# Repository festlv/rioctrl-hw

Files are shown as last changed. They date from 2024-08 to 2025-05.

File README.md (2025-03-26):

# rioctrl- a modular hardware for riocore

rioctrl is modular open source CNC controller hardware for [riocore](https://github.com/multigcs/riocore/).

It consists of a main FPGA controller board which has 6 slots for various input/output modules.

At this time, the following modules have been designed:

* [rioctrl-controller](rioctrl-controller/README.md): Lattice ECP5 based controller board
* [rioctrl-stepdir4](rioctrl-stepdir4/README.md): 4 axis step/dir output interface
* [rioctrl-quadenc4](rioctrl-quadenc4/README.md): 4 axis quadrature encoder (ABZ) input
* [rioctrl-shifio](rioctrl-shiftio/README.md): 16 digital inputs, 16 digital outputs (PNP)
* breakouts/lichuan-lc10: breakout board that allows connecting Lichuan LC10 series servo to stepdir4 and quadenc4 module (via off-the-shelf RJ45 cables)
* breakouts/rj45-screw-terminals: breakout board from RJ45 cable to screw terminals
* breakouts/ditron-dc11-encoder: breakout board from RJ45 cable to Ditron DC11 glass scale optical encoder (DB9)

# Current state of the hardware design

The following hardware has been built and tested to be working:

* rioctrl-controller v1.0: minor rework was needed (remove a diode, rotate Y1 by 90 degrees). Fixed in v1.1.
* rioctrl-stepdir4 v1.0: electrically working, mechanically a connector was offset by 4 mm, fixed in v1.1.
* rioctrl-shiftio: working as designed.
* rioctrl-quadencz: working as designed (with the caveat that it's only compatible with differential/RS422 encoders).
* breakouts/ditron-dc11-encoder: working as designed, tested with Ditron DC11 encoder with RS422 output option.
* breakouts/rj45-screw-terminals: working as designed.
* breakouts/lichuan-lc10: step/dir/enable working as designed, GPIOs not tested yet.

## Known issues

* External override for slot enable is slow to turn off stepdir enable signals. Need to scope this a bit, but it's either due to U14 output being
  tri-stated or the capacitance of +24V_EN lines powering the enable signals for some additional time.
# Pretty images

### rioctrl-controller
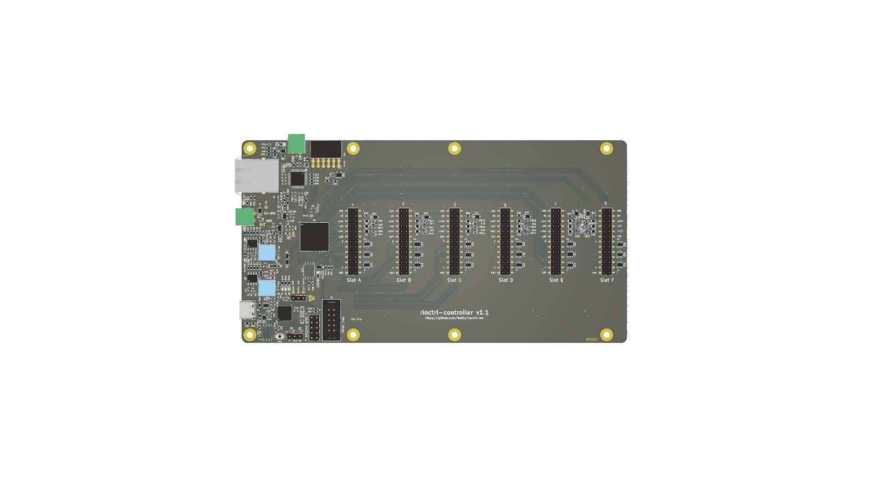
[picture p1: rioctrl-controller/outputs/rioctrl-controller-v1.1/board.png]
rioctrl-controller


### rioctrl-stepdir4
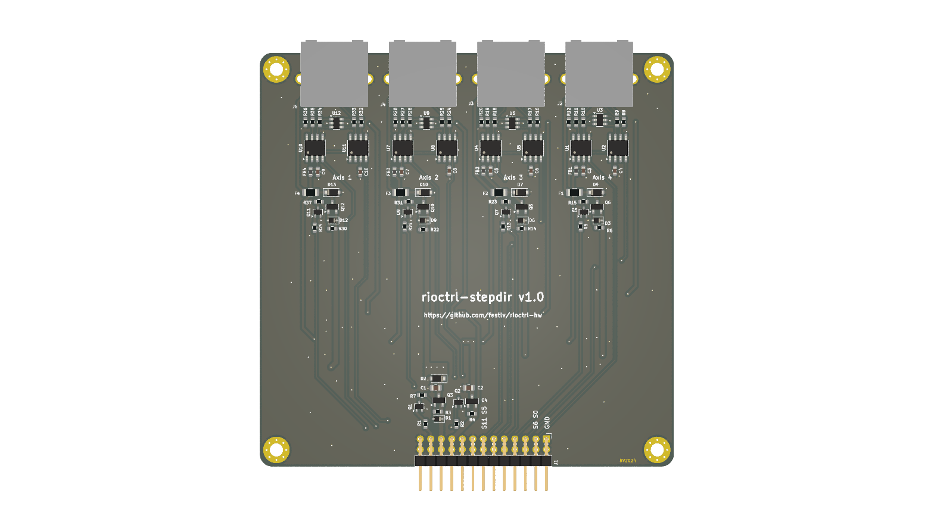
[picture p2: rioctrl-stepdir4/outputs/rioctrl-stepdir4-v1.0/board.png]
rioctrl-stepdir4


### rioctrl-quadenc4
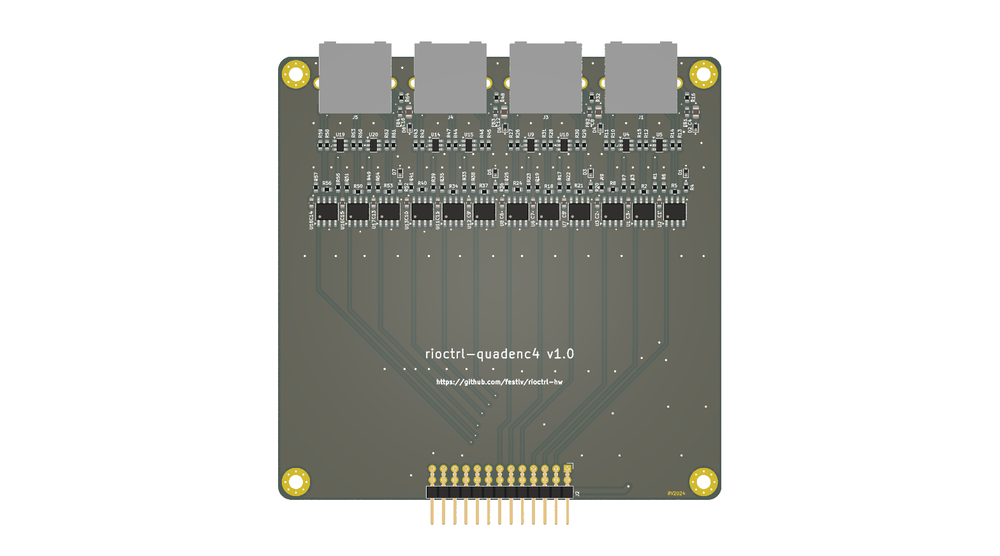
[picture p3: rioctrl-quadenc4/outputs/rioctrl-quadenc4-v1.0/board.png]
rioctrl-quadenc4


### rioctrl-shiftio
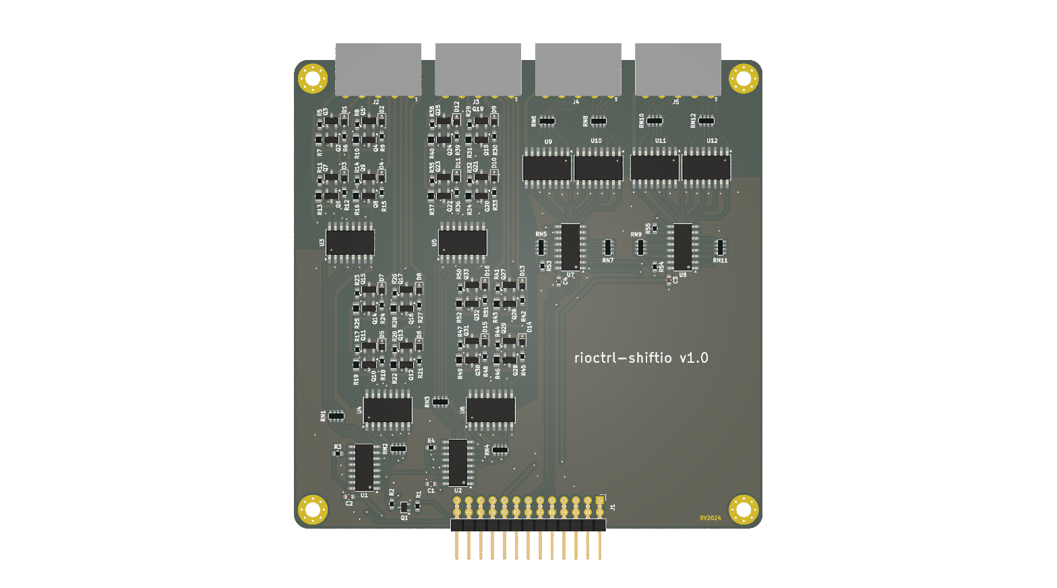
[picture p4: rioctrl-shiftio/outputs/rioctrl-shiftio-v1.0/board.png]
rioctrl-shiftio


### breakouts/lichuan-lc10
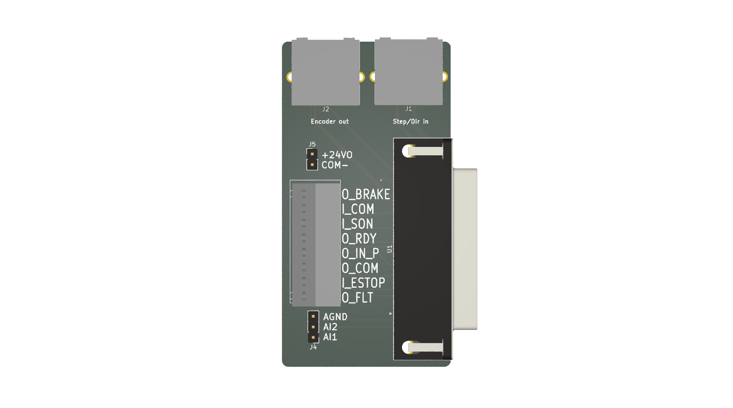
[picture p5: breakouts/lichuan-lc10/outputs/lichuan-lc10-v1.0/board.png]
breakouts/lichuan-lc10


### breakouts/rj45-screw-terminals
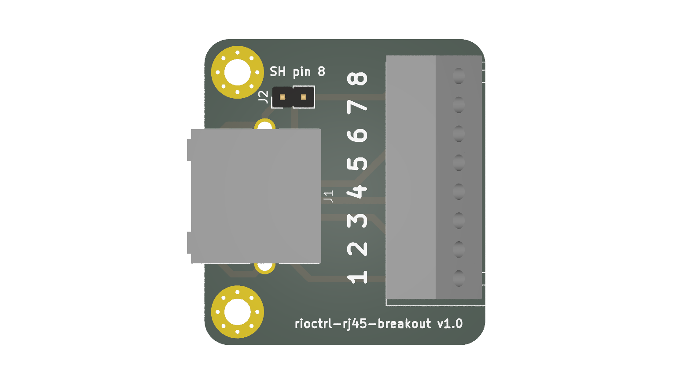
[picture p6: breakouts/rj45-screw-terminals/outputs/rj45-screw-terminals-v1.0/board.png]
breakouts/rj45-screw-terminals


## build.py

There is a `build.py` script that publishes outputs to each module `outputs` directory. It uses `<module>/version` file to
determine the current version, which should be updated accordingly.

For 3D renders of the boards, kicad-nightly package is needed, as the currently stable kicad version does not have board rendering functionality available from command line.

# License

The hardware designs in this repository are licensed under [CERN Open Hardware Licence Version 2 - Strongly Reciprocal](LICENSE.md).

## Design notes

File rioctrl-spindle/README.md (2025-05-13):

# rioctrl-spindle
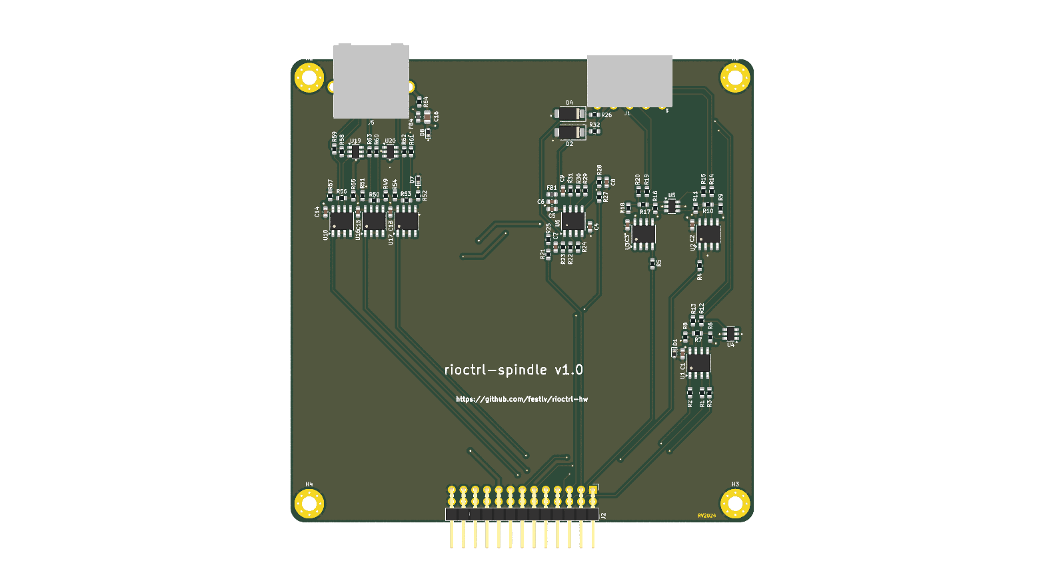
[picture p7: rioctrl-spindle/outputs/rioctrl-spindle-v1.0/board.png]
rioctrl-spindle


This module provides:
* 2 analog outputs (0..10V)
* RS-485 interface for Modbus
* RS-422 interface (for full-duplex serial communication, pending software support)
* Differential encoder interface

__Only analog outputs and Modbus has been tested!__

## Pinout

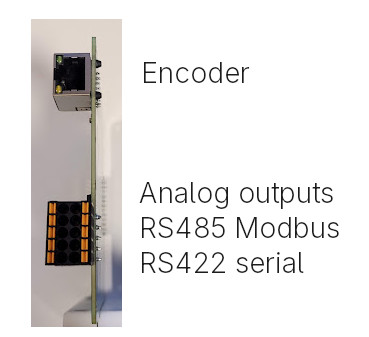
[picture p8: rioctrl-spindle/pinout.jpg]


| | |
|---|---|
| AIN0  | GND |
| AIN1  | SER_TX_A |
| MODBUS_A | SER_TX_B |
| MODBUS_B | SER_RX_A |
| x | SER_RX_B |

# Changelog

## v1.0
Initial released version.

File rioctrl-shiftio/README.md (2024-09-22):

# rioctrl-shiftio
rioctrl-shiftio

This module provides the following IOs:
* 16 opto-isolated digital outputs (PNP, external voltage input 5-24V in two groups). Each output is capable of sourcing ~0.6A of current and has over-current protection.
* 16 opto-isolated digital inputs (12-24V, both sourcing and sinking connections are possible).

Due to slot width limitations, each group of outputs (4 in total) are fitted with spring-type pluggable terminal blocks (LCSC part number:
[C2908401](https://www.lcsc.com/product-detail/Pluggable-System-Terminal-Block_JILN-JL15EDGKNH-35005B01_C2908401.html)).

# Pinout
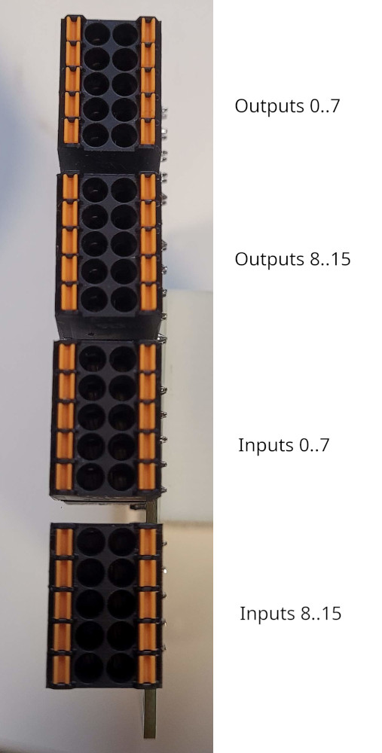
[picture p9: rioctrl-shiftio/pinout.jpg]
pinout


## Pinout of output blocks

VCC is 5..24V DC. Each of the output blocks has a separate power supply, so for example
one block can be 5V outputs and another one- 24VDC.

| VCC  | GND  |
|---|---|
| 0 | 1 |
| 2 | 3 |
| 4 | 5 |
| 6 | 7 |

| VCC | GND |
|-----|-----|
| 8 | 9 |
| 10  | 11  |
| 12  | 13  |
| 14  | 15  |

## Pinout of input blocks

Common input can be either ground, or positive voltage of 12..24VDC for sourcing or 
sinking type outputs.

Limited testing has shown that inputs also work at 5V output level, but that's not really guaranteed with the
values of components in current design.

| | Common |
|---|---|
| 0 | 1 |
| 2 | 3 |
| 4 | 5 |
| 6 | 7 |

|  | Common |
|-----|---|
| 8 | 9 |
| 10  | 11 |
| 12  | 13 |
| 14  | 15 |

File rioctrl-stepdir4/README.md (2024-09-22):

# rioctrl-stepdir4
rioctrl-stepdir4

This module provides 4 axis of step/dir/enable signals.
* Step/dir signals are differential 5V.
* Enable signal is at the same voltage as controller's DC input.

The connectors are RJ45 (intended use is either with motor-drive specific breakout board or a generic screw-terminal type breakout board).

RJ45 green LED is wired to enable signal.

## Pinout (when using breakouts/rioctrl-rj45-breakout):

| Pin | Signal |
|-----|---|
| 1 | Step + |
| 2 | Step - |
| 3 | Dir -  |
| 4 | Enable |
| 5 | GND |
| 6 | Dir -  |
| 7 | GND |
| 8 | GND |

# Changelog

## v1.1
* Fixed slot's pin-header position (was offset by 4 mm)
* Rename silkscreen labels from axis 1..4 to join 0..3 to match riocore/LinuxCNC convention
 
## v1.0
Initial released version.

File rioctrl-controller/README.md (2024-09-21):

# rioctrl-controller
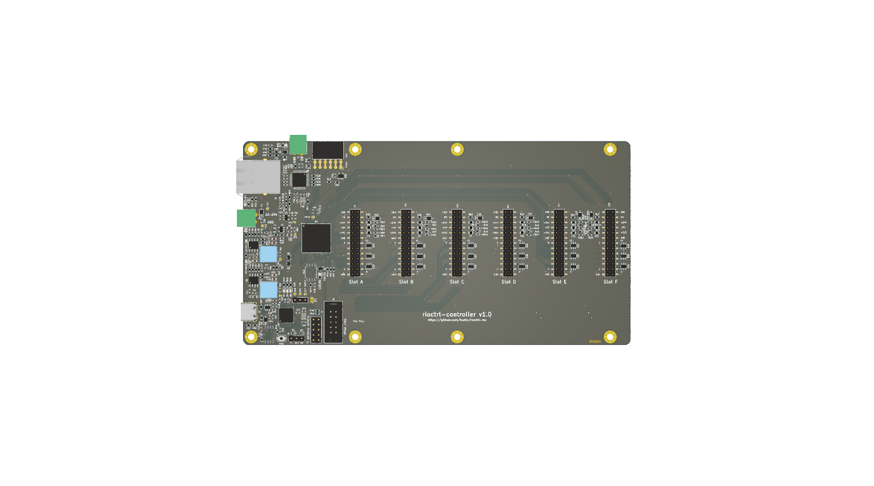
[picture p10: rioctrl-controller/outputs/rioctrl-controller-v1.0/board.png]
rioctrl-controller


The heart of controller is Lattice ECP5-series FPGA with 25k logic cells.

It has the following inputs/outputs:

* RJ45 Ethernet interface to PC (via Wiznet W5500)
* USB TypeC for re-flashing the FPGA (using RP2040 microcontroller with [pico-dirtyJtag](https://github.com/phdussud/pico-dirtyJtag) firmware)
* 12-24V DC input for powering the FPGA and basic slot hardware
* E-Stop signal that inhibits slot outputs in hardware, independant of FPGA gateware
* PMOD header for future expansion (e.g. controlling the board via SPI from RaspberryPi or something)
* JTAG header for FPGA debugging
* SWD header for JTAG probe debugging :)
* Six 2x13 pin 2.54mm sockets for slots (each has 12 FPGA signals, additional shared enable signal, +3.3V, +5V and input DC power)

Slot specification:
* Preferred slot PCB size: 100x100mm
* There are 12 FPGA signals wired to each slot, all of them are 3.3V.
* The following power rails are wired to each slot:
  * 3.3V
  * 5V
  * Input DC (12-24V)
* Each slot has an enable signal, whose state is a logical AND of FPGA enable output (watchdog-protected when using riocore) and external EStop input.
* Each slot **MUST** inhibit it's outputs in hardware when the enable signal is low.

# Changelog

## V1.0 -> V1.1
* Fix Y1 orientation
* DNP the USB VBUS -> 5V diode (it's useless, as 3.3V rails are generated by input voltage)
* Change LED:OK to green
 
# Bringup notes

* Build and flash the default configuration of pico-dirtyJtag (hold the boot button while turning on 12V power, then connect USB and flash via copying .uf2 to removable drive).
* Try to see if the FPGA is detected:
```
$ openFPGALoader -c dirtyJtag --detect

Jtag frequency : requested 6000000Hz -> real 6000000Hz
index 0:
	idcode 0x41111043
	manufacturer lattice
	family ECP5
	model  LFE5U-25
	irlength 8
```

# Version 1.0 rework
* Y1 needs to be rotated 90 degrees (again, sigh)
* Remove the D9 diode (USB power does not work anyway)
* Change D12 to green LED

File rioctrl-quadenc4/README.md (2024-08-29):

# rioctrl-quadenc4
rioctrl-quadenc4

This module provides 4 axis of differential quadrature encoder inputs, intended for 5V differential output encoders.
Each axis has A, B and Z inputs.

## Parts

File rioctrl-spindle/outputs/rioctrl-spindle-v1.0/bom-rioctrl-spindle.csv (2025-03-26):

Refs | Value | Footprint | Manufacturer | MPN | Qty | DNP | LCSC#
C1-C3,C6,C13-C15 | 0.1uF | Capacitor_SMD:C_0603_1608Metric |  |  | 7 |  | -- mixed values --
C4,C8 | 3.3nF | Capacitor_SMD:C_0603_1608Metric |  |  | 2
C5 | 10uF | Capacitor_SMD:C_0603_1608Metric |  |  | 1
C7,C9 | 10nF | Capacitor_SMD:C_0603_1608Metric |  |  | 2
C16 | 10uF | Capacitor_SMD:C_0805_2012Metric |  | GRM21BR61H106KE43L | 1 |  | C440198
D1,D7 | BSD5C031V | Diode_SMD:D_SOD-523 | BORN | BSD5C031V | 2 |  | C151984
D2,D4 | SMAJ10A | Diode_SMD:D_SMA |  |  | 2
D8 | PESD5V0S1BBN | Diode_SMD:D_SOD-523 | BORN | PESD5V0S1BBN | 1 |  | C314264
FB1,FB4 | FB_100R_3A | Inductor_SMD:L_0603_1608Metric | Sunlord | UPZ1608E101-3R0TF | 2 |  | C96995
J1 | TERM-BLK-02x05 | hadv-connectors:JL15EDGRHC-35005B02 | JILN | JL15EDGRHC-35005B02 | 1 |  | C2908411
J2 | Conn_02x13_Odd_Even | Connector_PinHeader_2.54mm:PinHeader_2x13_P2.54mm_Horizontal |  |  | 1 |  | C2894993
J5 | RJ45_LED_Shielded | hadv-connectors:R-RJ45R08P-C000 | Ckmtw(Shenzhen Cankemeng) | R-RJ45R08P-C000 | 1 |  | C386757
R1,R6,R8,R9,R11,R16,R18,R49,R51,R52,R54,R55,R57 | 1K | Resistor_SMD:R_0603_1608Metric |  |  | 13 |  | C22548
R2-R5,R12-R15,R19,R20,R58-R63 | 10R | Resistor_SMD:R_0603_1608Metric |  |  | 16 |  | C109318
R7,R10,R17,R50,R53,R56 | 120R | Resistor_SMD:R_0603_1608Metric |  |  | 6 |  | C114640
R21-R24,R27,R29-R31 | 10K | Resistor_SMD:R_0603_1608Metric |  |  | 8
R25,R28 | 100K | Resistor_SMD:R_0603_1608Metric |  |  | 2
R26,R32 | 50R | Resistor_SMD:R_0603_1608Metric |  |  | 2
R64 | 0R | Resistor_SMD:R_0603_1608Metric |  |  | 1 |  | C95177
U1-U3,U16-U18 | CS48505S | Package_SO:SOIC-8_3.9x4.9mm_P1.27mm | Chipanalog | CS48505S | 6 |  | C3202824
U4,U5,U19,U20 | USBLC6-4SC6 | Package_TO_SOT_SMD:SOT-23-6 | TECH PUBLIC | USBLC6-4SC6 | 4 |  | C5197386
U6 | LM358DT | Package_SO:SO-8_3.9x4.9mm_P1.27mm | STMicroelectronics | LM358DT | 1 |  | C9418

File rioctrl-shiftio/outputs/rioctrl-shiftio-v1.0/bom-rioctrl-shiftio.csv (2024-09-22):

Refs | Value | Footprint | Manufacturer | MPN | Qty | DNP | LCSC#
C1-C4 | 0.1uF | Capacitor_SMD:C_0603_1608Metric |  |  | 4 |  | C14663
D1-D16 | 1N4007WS | Diode_SMD:D_SOD-323F | MKSEMI | 1N4007WS | 16 |  | C7528872
J1 | Conn_02x13_Odd_Even | Connector_PinHeader_2.54mm:PinHeader_2x13_P2.54mm_Horizontal |  |  | 1 |  | C2894993
J2-J5 | TERM-BLK-02x05 | hadv-connectors:JL15EDGRHC-35005B02 | JILN | JL15EDGRHC-35005B02 | 4 |  | C2908411
Q1 | BSS138W | Package_TO_SOT_SMD:SOT-323_SC-70 | Jiangsu Changjing Electronics Technology Co., Ltd. | BSS138W | 1 |  | C504052
Q2,Q4,Q6,Q8,Q10,Q12,Q14,Q16,Q18,Q20,Q22,Q24,Q26,Q28,Q30,Q32 | MMBT3906 | Package_TO_SOT_SMD:SOT-23 | TWGMC | MMBT3906 | 16 |  | C727128
Q3,Q5,Q7,Q9,Q11,Q13,Q15,Q17,Q19,Q21,Q23,Q25,Q27,Q29,Q31,Q33 | AO3401A | Package_TO_SOT_SMD:SOT-23 | UMW | AO3401A | 16 |  | C347476
R1,R3,R4,R6,R9,R12,R15,R18,R21,R24,R27,R30,R33,R36,R39,R42,R45,R48,R51,R53-R55 | 10K | Resistor_SMD:R_0603_1608Metric |  |  | 22 |  | C98220
R2 | 4K7 | Resistor_SMD:R_0603_1608Metric |  |  | 1 |  | C99782
R5,R8,R11,R14,R17,R20,R23,R26,R29,R32,R35,R38,R41,R44,R47,R50 | 47K | Resistor_SMD:R_0603_1608Metric |  |  | 16 |  | C105579
R7,R10,R13,R16,R19,R22,R25,R28,R31,R34,R37,R40,R43,R46,R49,R52 | 1R | Resistor_SMD:R_0805_2012Metric |  |  | 16 |  | C131397
RN1-RN4 | 220R | Resistor_SMD:R_Array_Convex_4x0603 |  |  | 4 |  | C706474
RN5-RN12 | 4.12K | Resistor_SMD:R_Array_Convex_4x0603 |  |  | 8 |  | C728970
U1,U2 | 74HC595 | Package_SO:SO-16_3.9x9.9mm_P1.27mm | Nexperia | 74HC595D,118 | 2 |  | C5947
U3-U6,U9-U12 | ELQ3H4 | Package_SO:SOIC-16W_5.3x10.2mm_P1.27mm | Everlight Elec | ELQ3H4(TA)-G | 8 |  | C150957
U7,U8 | 74HC165 | Package_SO:SO-16_3.9x9.9mm_P1.27mm | Nexperia | 74HC165D,653 | 2 |  | C5613

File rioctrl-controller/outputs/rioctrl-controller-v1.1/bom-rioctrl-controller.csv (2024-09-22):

Refs | Value | Footprint | Manufacturer | MPN | Qty | DNP | LCSC#
C1-C3 | 10uF | Capacitor_SMD:C_0805_2012Metric | -- mixed values -- | -- mixed values -- | 3 |  | C440198
C4,C5,C12-C14,C21,C24,C25,C27-C32,C36,C40-C42,C55 | 0.1uF | Capacitor_SMD:C_0603_1608Metric | -- mixed values -- | -- mixed values -- | 19 |  | C14663
C6,C7 | 120pF | Capacitor_SMD:C_0603_1608Metric |  |  | 2 |  | C107035
C8,C9 | 0.012uF | Capacitor_SMD:C_0603_1608Metric |  |  | 2 |  | C282672
C10 | DNP | Capacitor_SMD:C_0603_1608Metric |  |  | 1 | DNP
C11 | 10uF/35V | Capacitor_SMD:C_0805_2012Metric | Murata | GRM21BR6YA106ME43L | 1 |  | C440198
C15-C18 | 47uF | Capacitor_SMD:C_0805_2012Metric |  | GRM21BR61H106KE43L | 4 |  | C6119904
C19,C20,C26 | 1uF | Capacitor_SMD:C_0603_1608Metric | -- mixed values -- | -- mixed values -- | 3 |  | C5673
C22,C23 | 10pF | Capacitor_SMD:C_0603_1608Metric | Yageo | CC0603JRNPO9BN100 | 2 |  | C106245
C33,C34 | 18pF | Capacitor_SMD:C_0603_1608Metric |  |  | 2 |  | C92671
C35,C39 | 10uF/6.3V | Capacitor_SMD:C_0603_1608Metric |  |  | 2 |  | C85713
C37,C46 | 10nF | Capacitor_SMD:C_0603_1608Metric |  |  | 2 |  | C100042
C38 | 4.7uF | Capacitor_SMD:C_0603_1608Metric |  |  | 1 |  | C1705
C43 | 22nF | Capacitor_SMD:C_0603_1608Metric |  |  | 1 |  | C77571
C44,C45 | 6.8nF | Capacitor_SMD:C_0603_1608Metric |  |  | 2 |  | C1631
C47-C54,C56-C67 | 0.1uF | Capacitor_SMD:C_0402_1005Metric |  |  | 20 |  | C56392
D1,D9 | DSS34 | Diode_SMD:D_SOD-123F | BORN | DSS34 | 2 | -- mixed values -- | C511866
D2,D4,D10,D17 | LED_RED | LED_SMD:LED_0603_1608Metric | Yongyu Photoelectric | SZYY0603R | 4 |  | C434419
D3,D11,D12 | LED_GREEN | LED_SMD:LED_0603_1608Metric | Yongyu Photoelectric | SZYY0603YG | 3 |  | C434423
D5 | LED_BLUE | LED_SMD:LED_0603_1608Metric | XINGLIGHT | XL-1608UBC-04 | 1 |  | C965807
D6-D8,D14,D19,D22,D25,D28,D31 | BSD5C031V | Diode_SMD:D_SOD-523 | BORN | BSD5C031V | 9 |  | C151984
D13,D18,D21,D24,D27,D30 | SMF24A | Diode_SMD:D_SOD-123F | Shandong Jingdao Microelectronics | SMF24A | 6 |  | C169430
D15,D16,D20,D23,D26,D29,D32 | PESD5V0S1BBN | Diode_SMD:D_SOD-523 | BORN | PESD5V0S1BBN | 7 |  | C314264
F1-F18 | SMD0805B050TF | Fuse:Fuse_0805_2012Metric | Yageo | SMD0805B050TF | 18 |  | C269104
FB1-FB25 | FB_100R_3A | Inductor_SMD:L_0603_1608Metric | Sunlord | UPZ1608E101-3R0TF | 25 |  | C96995
J1,J7 | TERM-BLK-2H | Connector_Phoenix_MC:PhoenixContact_MC_1,5_2-G-3.5_1x02_P3.50mm_Horizontal | Cixi Kefa Elec | KF2EDGR-3.5-2P | 2 |  | C441171
J2,J5 | PIN_HEADER_3V | Connector_PinHeader_2.54mm:PinHeader_1x03_P2.54mm_Vertical | Boom Precision Elec | C49257 | 2 |  | C49257
J3 | TYPE-C-31-M-12 | hadv-connectors:USB_C_Receptacle_HRO_TYPE-C-31-M-12 | Korean Hroparts | TYPE-C-31-M-12 | 1 |  | C165948
J4 | Conn_02x05_Odd_Even | Connector_PinHeader_2.54mm:PinHeader_2x05_P2.54mm_Vertical |  |  | 1 | DNP
J6 | RJ45_Pulse_J0011D21BNL | hadv-connectors:RJ45_J0011D21BNL | Pulse | J0011D21BNL | 1 |  | C455444
J8 | Conn_02x05_PH | Connector_IDC:IDC-Header_2x05_P2.54mm_Vertical |  |  | 1 |  | C5665
J9,J11-J15 | Conn_02x13_Odd_Even | Connector_PinSocket_2.54mm:PinSocket_2x13_P2.54mm_Vertical_SMD |  |  | 6 |  | C3975158
J10 | Conn_02x06_Odd_Even | Connector_PinSocket_2.54mm:PinSocket_2x06_P2.54mm_Horizontal |  |  | 1 |  | C2897426
L1 | MLP2012S4R7MT0S1 | Inductor_SMD:L_0805_2012Metric | TDK | MLP2012S4R7MT0S1 | 1 |  | C87543
L2,L3 | PSPMAA0805-220M-ANP | hadv-inductors:SMD_INDUCTOR_8x8.5x5mm | PROD Tech | PSPMAA0805-220M-ANP | 2 |  | C2962887
Q1-Q4 | BSS138W | Package_TO_SOT_SMD:SOT-323_SC-70 | Jiangsu Changjing Electronics Technology Co., Ltd. | BSS138W | 4 |  | C504052
R1,R17,R23,R27,R29-R32,R44-R49,R54 | 10K | Resistor_SMD:R_0603_1608Metric | -- mixed values -- | -- mixed values -- | 15 |  | C98220
R2,R3,R5,R7,R10 | 47K | Resistor_SMD:R_0603_1608Metric | -- mixed values -- |  | 5 |  | C105579
R4,R6 | 220K | Resistor_SMD:R_0603_1608Metric |  |  | 2 |  | C123420
R8,R9 | 3.47K | Resistor_SMD:R_0603_1608Metric |  |  | 2 |  | C273778
R11 | 56.2K | Resistor_SMD:R_0603_1608Metric | Yageo | RC0603FR-0710KL | 1 |  | C98220
R12,R14,R26 | 100K | Resistor_SMD:R_0603_1608Metric | -- mixed values -- | -- mixed values -- | 3 |  | C112314
R13 | 19.1K | Resistor_SMD:R_0603_1608Metric |  |  | 1 |  | C173754
R15 | 32K | Resistor_SMD:R_0603_1608Metric |  |  | 1 |  | C861839
R16,R18,R19,R28,R55 | 1K | Resistor_SMD:R_0603_1608Metric | -- mixed values -- | -- mixed values -- | 5 |  | C22548
R20-R22 | 5.11K | Resistor_SMD:R_0603_1608Metric | Yageo | RC0603FR-075K11L | 3 |  | C112314
R24 | 1M | Resistor_SMD:R_0603_1608Metric |  |  | 1 |  | C107698
R25 | 12.4K | Resistor_SMD:R_0603_1608Metric |  |  | 1 |  | C22865
R33,R34,R50-R52,R56 | 330R | Resistor_SMD:R_0603_1608Metric |  |  | 6 |  | C105881
R35-R38 | 0R | Resistor_SMD:R_0603_1608Metric |  |  | 4 |  | C95177
R39,R40,R42,R43 | 49.9R | Resistor_SMD:R_0603_1608Metric |  |  | 4 |  | C114625
R41 | 10R | Resistor_SMD:R_0603_1608Metric |  |  | 1 |  | C109318
R53,R58-R62 | 100R | Resistor_SMD:R_0603_1608Metric |  |  | 6 |  | C105588
R57,R63 | 4K7 | Resistor_SMD:R_0603_1608Metric |  |  | 2 |  | C99782
SW1 | SW_PUSH_SMALL | hadv-ui:SW_SPST_AR02016 | XUNPU | TS-1088-AR02016 | 1 |  | C720477
U1 | TD6811 | Package_TO_SOT_SMD:SOT-23-5 | Techcode | TD6811 | 1 |  | C189486
U2,U3 | TPS54335ADDAR | Package_SO:SOIC-8-1EP_3.9x4.9mm_P1.27mm_EP2.29x3mm_ThermalVias | Texas Instruments | TPS54335ADDAR | 2 |  | C58928
U4 | NCP114ASN250T1G | Package_TO_SOT_SMD:SOT-23-5 | Onsemi | NCP114ASN250T1G | 1 |  | C892030
U5,U10 | W25Q16JVSS | Package_SO:SOIC-8_5.23x5.23mm_P1.27mm | Winbond | W25Q16JVSSIQ | 2 |  | C82317
U6 | USBLC6-4SC6 | Package_TO_SOT_SMD:SOT-23-6 | TECH PUBLIC | USBLC6-4SC6 | 1 |  | C5197386
U7 | RP2040 | hadv-mcu:RP2040-QFN-56 | Raspberry Pi | RP2040 | 1 |  | C2040
U8 | W5500 | Package_QFP:LQFP-48_7x7mm_P0.5mm |  |  | 1 |  | C32843
U9 | ECP5U_45_CABGA256 | Package_BGA:BGA-256_14.0x14.0mm_Layout16x16_P0.8mm_Ball0.45mm_Pad0.32mm_NSMD | Lattice | LFE5U-12F-6BG256C | 1 |  | C1550762
U11-U13,U15-U29 | SRV05-4 | Package_TO_SOT_SMD:SOT-23-6 | UMW(Youtai Semiconductor Co., Ltd.) | SRV05-4.TCT | 18 |  | C2687126
U14 | SN74LVC1G125DBV | Package_TO_SOT_SMD:SOT-23-5 | Texas Instruments | SN74LVC1G125DBVR | 1 |  | C23654
X1 | OSC_25MHz | Oscillator:Oscillator_SMD_EuroQuartz_XO32-4Pin_3.2x2.5mm | YXC Crystal Oscillators | OT322525MJBA4SL | 1 |  | C669088
Y1 | Crystal_12MHz | Crystal:Crystal_SMD_2520-4Pin_2.5x2.0mm | TAE(Zhejiang Abel Elec) | TXM12M0004252DBCEO00T | 1 |  | C284154
Y2 | Crystal_25MHz | Crystal:Crystal_SMD_2520-4Pin_2.5x2.0mm | Yajingxin | TXM25M0004252DBCEO00T | 1 |  | C284164

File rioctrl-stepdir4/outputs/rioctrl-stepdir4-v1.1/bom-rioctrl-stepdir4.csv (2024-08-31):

Refs | Value | Footprint | Manufacturer | MPN | Qty | DNP | LCSC#
C1,C2 | 10uF | Capacitor_SMD:C_0805_2012Metric |  | GRM21BR61H106KE43L | 2 |  | C440198
C3-C10 | 0.1uF | Capacitor_SMD:C_0603_1608Metric |  |  | 8 |  | C14663
D1,D3,D6,D9,D12 | BZT52C10S | Diode_SMD:D_SOD-323 | YFW | BZT52C10S | 5 |  | C5270769
D2,D4,D7,D10,D13 | SMF24A | Diode_SMD:D_SOD-123F | Shandong Jingdao Microelectronics | SMF24A | 5 |  | C169430
F1-F4 | BSMD1206-100-24V | Fuse:Fuse_1206_3216Metric | BHFUSE | BSMD1206-100-24V | 4 |  | C910830
FB1-FB4 | FB_100R_3A | Inductor_SMD:L_0603_1608Metric | Sunlord | UPZ1608E101-3R0TF | 4 |  | C96995
J1 | Conn_02x13_Odd_Even | Connector_PinHeader_2.54mm:PinHeader_2x13_P2.54mm_Horizontal |  |  | 1 |  | C2894993
J2-J5 | RJ45_LED_Shielded | hadv-connectors:R-RJ45R08P-C000 | Ckmtw(Shenzhen Cankemeng) | R-RJ45R08P-C000 | 4 |  | C386757
Q1,Q2,Q5,Q7,Q9,Q11 | BSS138W | Package_TO_SOT_SMD:SOT-323_SC-70 | Jiangsu Changjing Electronics Technology Co., Ltd. | BSS138W | 6 |  | C504052
Q3,Q4,Q6,Q8,Q10,Q12 | AO3401A | Package_TO_SOT_SMD:SOT-23 | UMW | AO3401A | 6 |  | C347476
R1-R7,R12-R15,R20-R23,R28-R31,R36,R37 | 10K | Resistor_SMD:R_0603_1608Metric |  |  | 21 |  | C98220
R8-R11,R16-R19,R24-R27,R32-R35 | 100R | Resistor_SMD:R_0603_1608Metric |  |  | 16 |  | C105588
U1,U2,U4,U5,U7,U8,U10,U11 | CS48505S | Package_SO:SOIC-8_3.9x4.9mm_P1.27mm | Chipanalog | CS48505S | 8 |  | C3202824
U3,U6,U9,U12 | USBLC6-4SC6 | Package_TO_SOT_SMD:SOT-23-6 | TECH PUBLIC | USBLC6-4SC6 | 4 |  | C5197386

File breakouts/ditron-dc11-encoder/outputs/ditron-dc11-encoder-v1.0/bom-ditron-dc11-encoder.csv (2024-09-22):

Refs | Value | Footprint | Manufacturer | MPN | Qty | DNP | LCSC#
J1 | DB9_Receptacle | Connector_Dsub:DSUB-9_Female_Horizontal_P2.77x2.84mm_EdgePinOffset7.70mm_Housed_MountingHolesOffset9.12mm | Ckmtw | D-DMR009PF-D002 | 1 |  | C141882
J2 | RJ45_LED_Shielded | hadv-connectors:R-RJ45R08P-C000 | Ckmtw(Shenzhen Cankemeng) | R-RJ45R08P-C000 | 1 |  | C386757
R1 | 3K3 | Resistor_SMD:R_0603_1608Metric |  |  | 1 |  | C108078

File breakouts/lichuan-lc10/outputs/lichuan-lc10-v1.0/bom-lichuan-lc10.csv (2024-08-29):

Refs | Value | Footprint | Manufacturer | MPN | Qty | DNP | LCSC#
J1,J2 | RJ45_LED_Shielded | hadv-connectors:R-RJ45R08P-C000 | Ckmtw(Shenzhen Cankemeng) | R-RJ45R08P-C000 | 2 |  | C386757
J3 | TERM-BLK-8H-S | hadv-connectors:MX250-3.5-08P-B | MAX | MX250-3.5-08P-B-GY01-Cu-A | 1 |  | C7470122
J4 | Conn_01x03 | Connector_PinHeader_2.54mm:PinHeader_1x03_P2.54mm_Vertical |  |  | 1
J5 | Conn_01x02 | Connector_PinHeader_2.54mm:PinHeader_1x02_P2.54mm_Vertical |  |  | 1
U1 | ~ | Connector_Dsub:DSUB-44-HD_Male_Horizontal_P2.29x1.98mm_EdgePinOffset8.35mm_Housed_MountingHolesOffset10.89mm | Connfly | DS1038-44MBNSIA74-0CC | 1 |  | C77845

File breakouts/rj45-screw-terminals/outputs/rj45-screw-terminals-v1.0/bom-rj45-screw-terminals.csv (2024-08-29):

Refs | Value | Footprint | Manufacturer | MPN | Qty | DNP | LCSC#
J1 | RJ45_LED_Shielded | hadv-connectors:R-RJ45R08P-C000 | Ckmtw(Shenzhen Cankemeng) | R-RJ45R08P-C000 | 1 |  | C386757
J2 | Conn_01x02 | Connector_PinHeader_2.54mm:PinHeader_1x02_P2.54mm_Vertical |  |  | 1
J3 | TERM-BLK-8H-S | hadv-connectors:MX250-3.5-08P-B | MAX | MX250-3.5-08P-B-GY01-Cu-A | 1 |  | C7470122

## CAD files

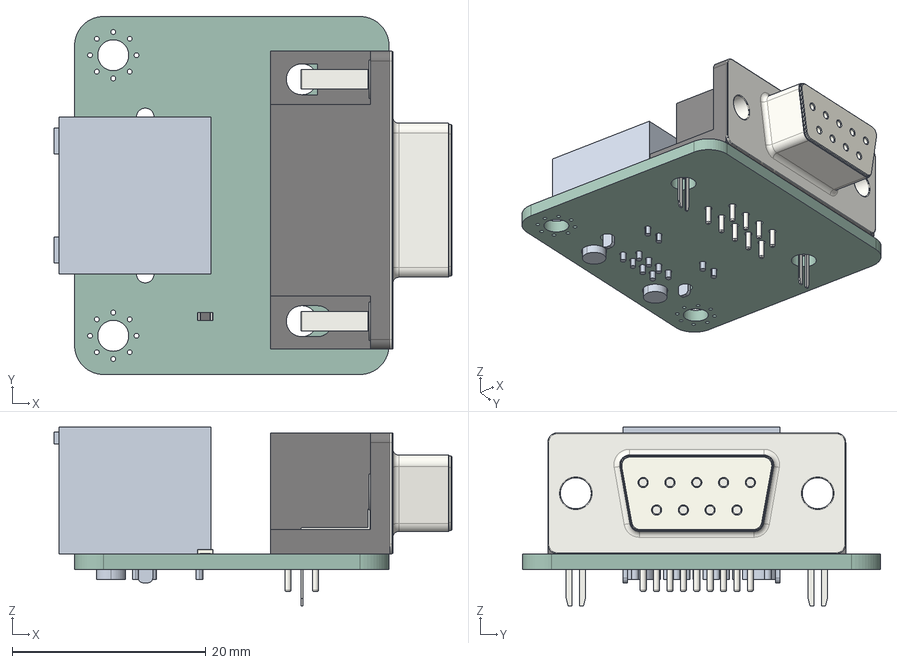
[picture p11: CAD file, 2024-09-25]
breakouts/ditron-dc11-encoder/outputs/ditron-dc11-encoder-v1.0/ditron-dc11-encoder.step
41.1 x 37.0 x 18.5 mm
DSUB-9_Female_Horizontal_P2.77x2.84mm_EdgePinOffset7.70mm_Housed_ MountingHolesOffset9.12mm
R_0603_1608Metric
R-RJ45R08P-C000
ditron-dc11-encoder_PCB

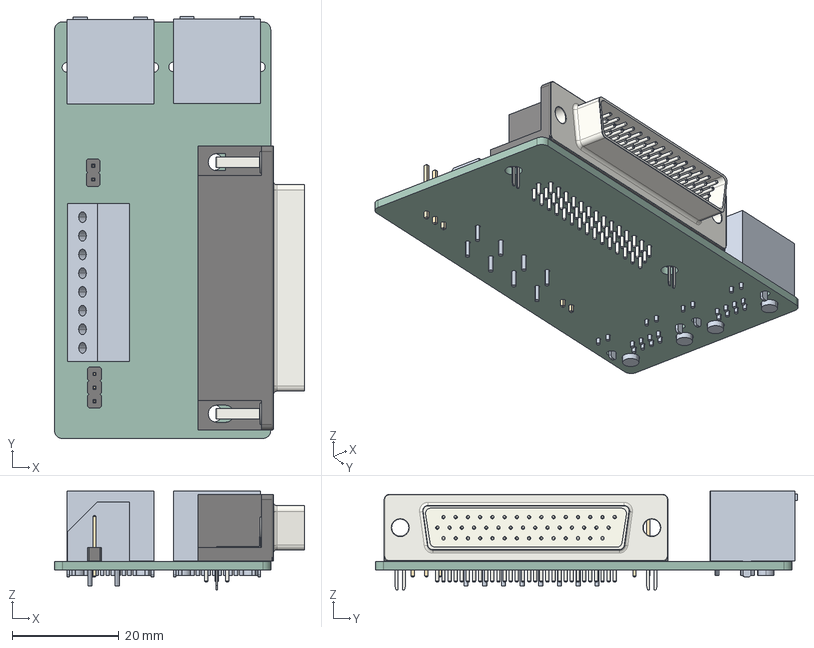
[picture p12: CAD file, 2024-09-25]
breakouts/lichuan-lc10/outputs/lichuan-lc10-v1.0/lichuan-lc10.step
46.8 x 79.0 x 18.5 mm
PinHeader_1x03_P254mm_Vertical
PinHeader_1x02_P254mm_Vertical
R-RJ45R08P-C000 x 2
MX250-3_5-08P-B-GY01-Cu-A
DSUB-44-HD_Male_Horizontal_P2.29x1.98mm_EdgePinOffset8.35mm_Housed_ MountingHolesOffset10.89mm
lichuan-lc10_PCB

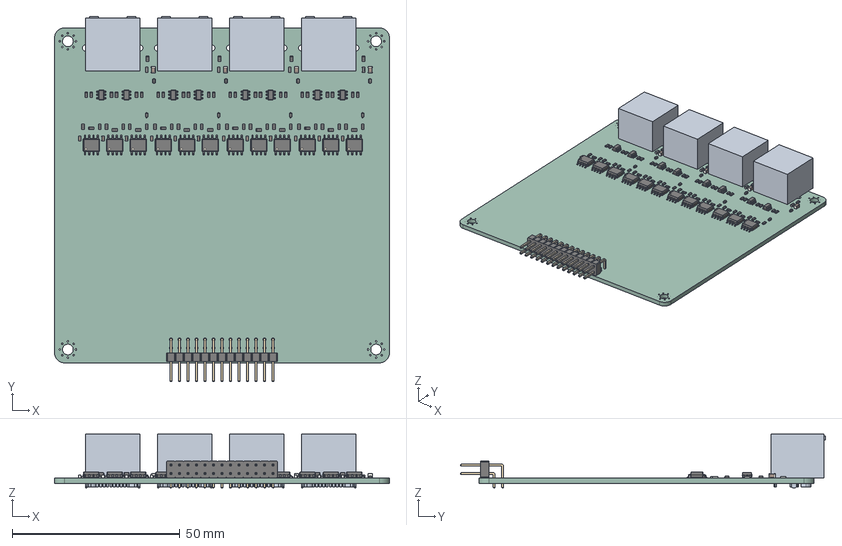
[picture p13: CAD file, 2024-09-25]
rioctrl-quadenc4/outputs/rioctrl-quadenc4-v1.0/rioctrl-quadenc4.step
100.0 x 109.0 x 16.1 mm
C_0603_1608Metric x 12
R_0603_1608Metric x 64
SOT_23_6 x 8
SOIC_8_39x49mm_P127mm x 12
C_0805_2012Metric x 4
D_SOD_523 x 8
PinHeader_2x13_P254mm_Horizontal
R-RJ45R08P-C000 x 4
L_0603_1608Metric x 4
rioctrl-quadenc4_PCB

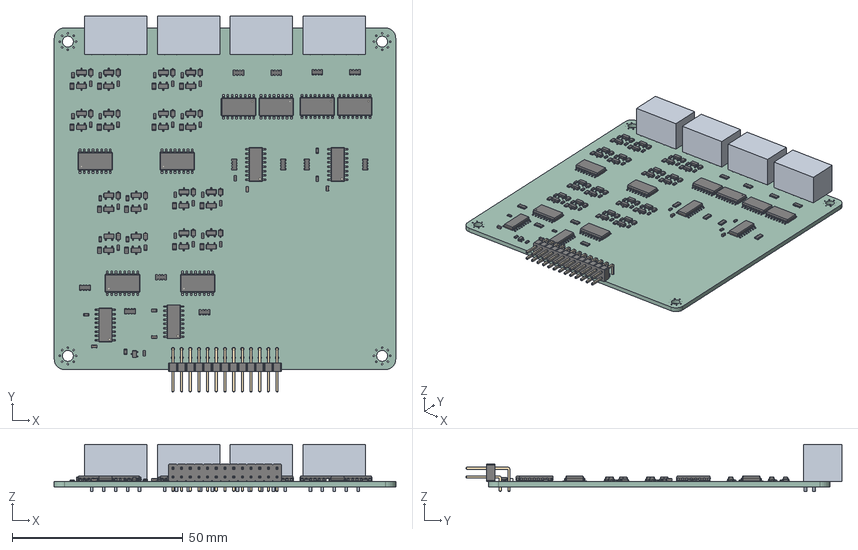
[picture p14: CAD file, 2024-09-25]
rioctrl-shiftio/outputs/rioctrl-shiftio-v1.0/rioctrl-shiftio.step
100.0 x 110.1 x 13.8 mm
SOT_23 x 32
R_0603_1608Metric x 39
D_SOD_323F x 16
SO-16_3.9x9.9mm_P1.27mm x 4
R_0805_2012Metric x 16
R_Array_Convex_4x0603 x 12
SOIC_16W_53x102mm_P127mm x 8
C_0603_1608Metric x 4
PinHeader_2x13_P254mm_Horizontal
JL15EDGRHC-35005B02 x 4
SOT_323_SC_70
rioctrl-shiftio_PCB

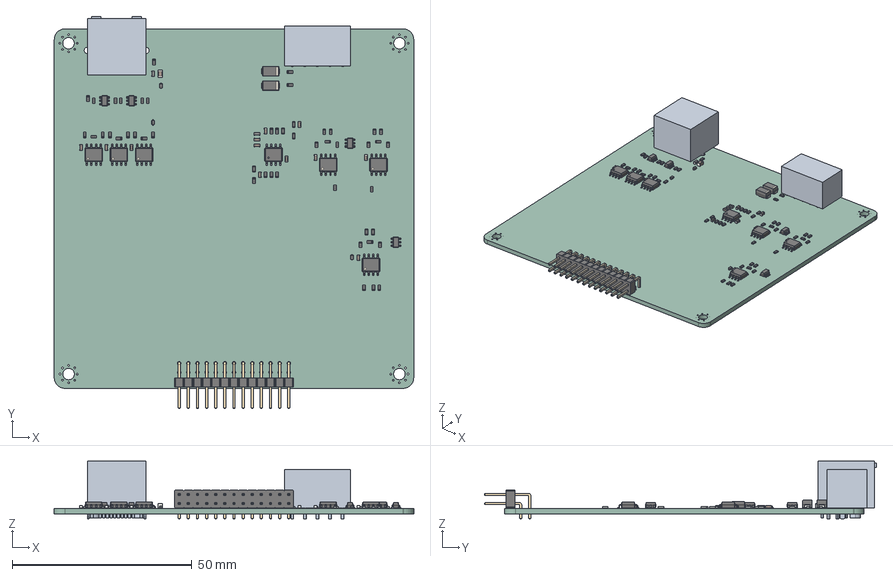
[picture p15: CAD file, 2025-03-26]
rioctrl-spindle/outputs/rioctrl-spindle-v1.0/rioctrl-spindle.step
100.0 x 109.0 x 16.1 mm
C_0603_1608Metric x 12
R_0603_1608Metric x 48
SOIC_8_39x49mm_P127mm x 6
D_SOD_523 x 3
PinHeader_2x13_P254mm_Horizontal
L_0603_1608Metric x 2
JL15EDGRHC-35005B02
D_SMA x 2
C_0805_2012Metric
SOT_23_6 x 4
R-RJ45R08P-C000
CQ assembly
rioctrl-spindle_PCB

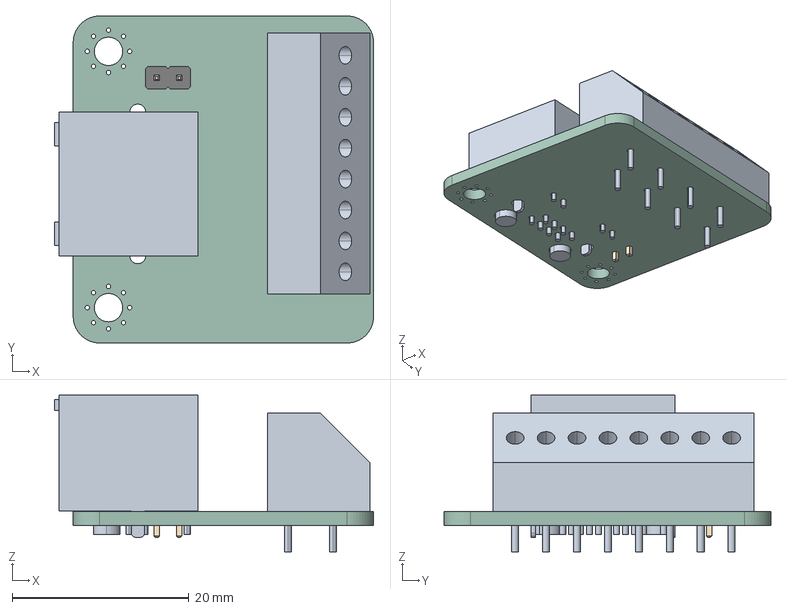
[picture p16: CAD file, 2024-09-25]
breakouts/rj45-screw-terminals/outputs/rj45-screw-terminals-v1.0/rj45-screw-terminals.step
36.1 x 37.0 x 17.8 mm
R-RJ45R08P-C000
PinHeader_1x02_P254mm_Vertical
MX250-3_5-08P-B-GY01-Cu-A
rj45-screw-terminals_PCB

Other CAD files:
rioctrl-stepdir4/outputs/rioctrl-stepdir4-v1.1/rioctrl-stepdir4.step
rioctrl-stepdir4/outputs/rioctrl-stepdir4-v1.0/rioctrl-stepdir4.step

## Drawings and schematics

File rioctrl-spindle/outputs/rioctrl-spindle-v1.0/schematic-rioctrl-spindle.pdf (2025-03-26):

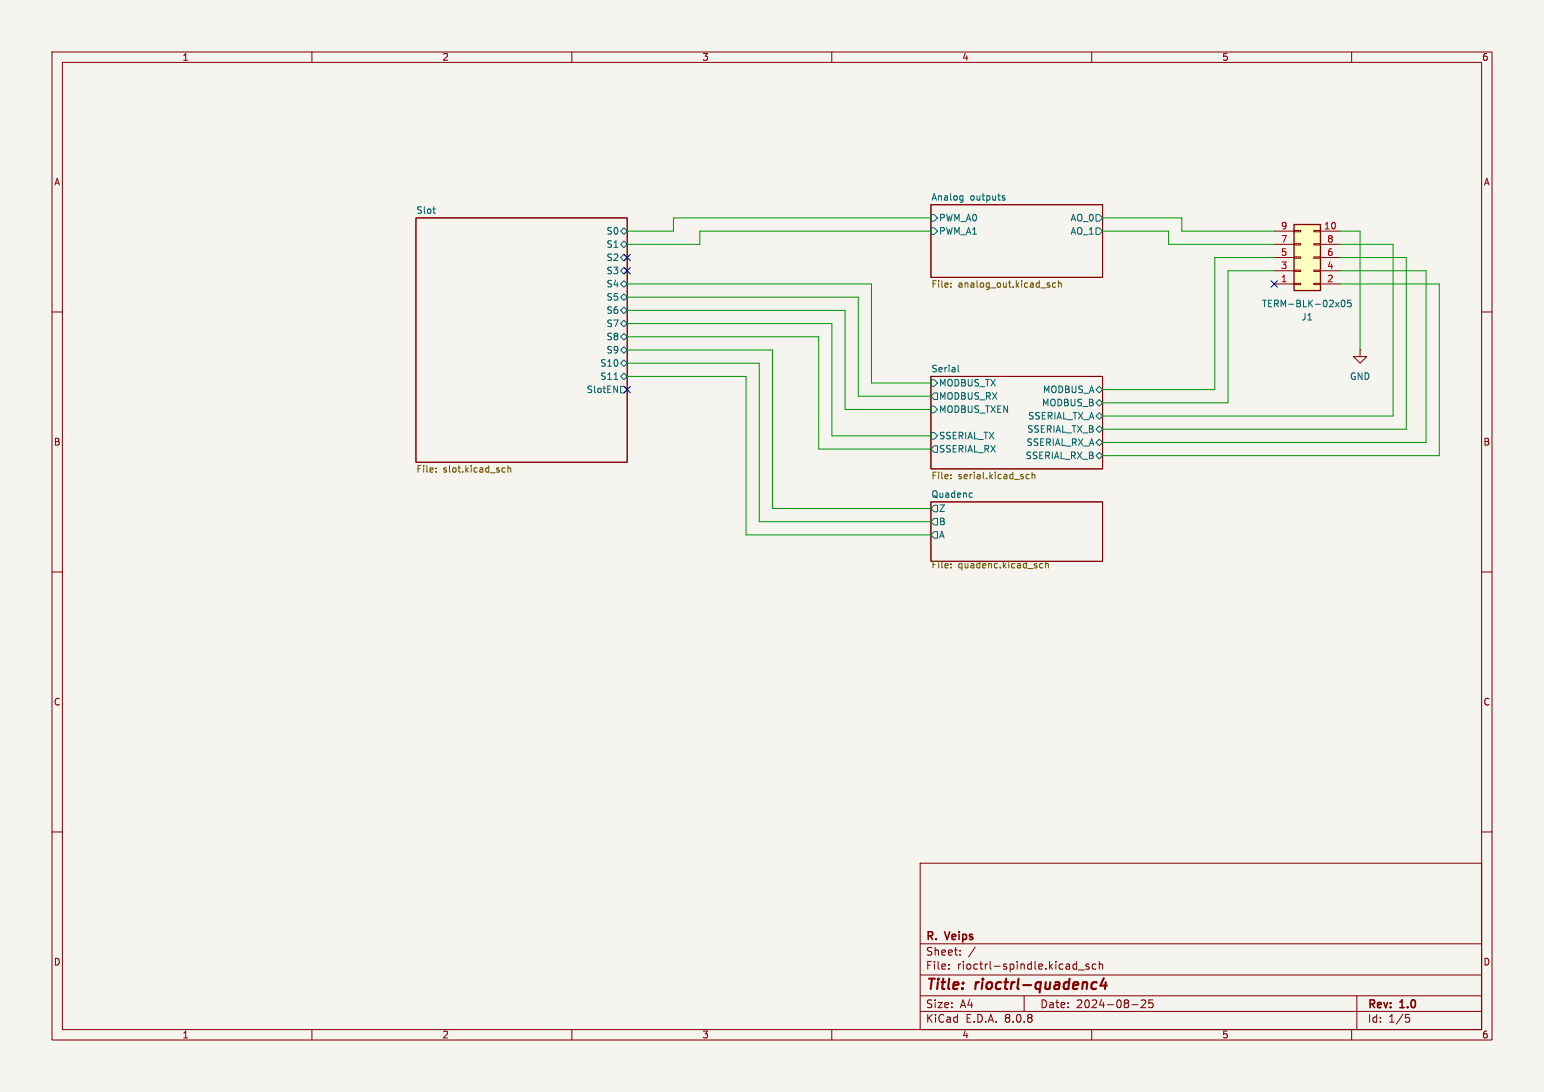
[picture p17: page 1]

Serial File: serial.kicad_sch S0S4S1S5S2S3S6S8S7S9 S11 S10 SlotEN

File: rioctrl-spindle.kicad_sch Sheet: / R. Veips

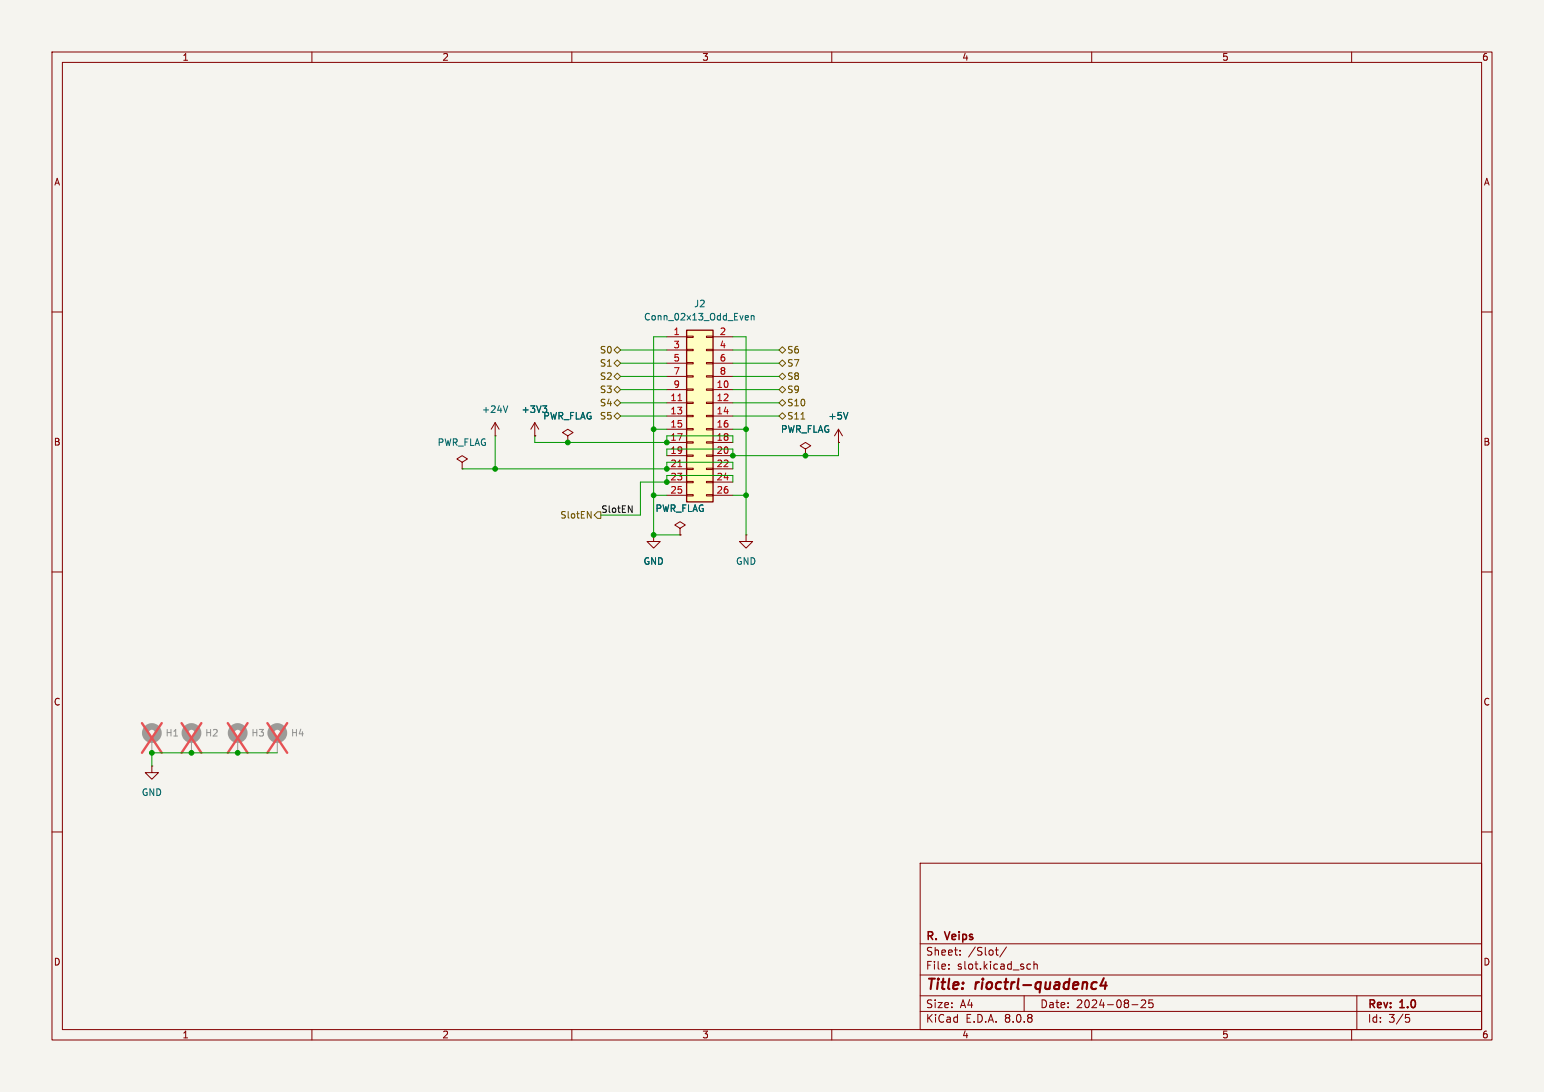
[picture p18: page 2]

3 5 7 9 11 13 15 | 4 6 8 10 12 14 16 | S6S8S9S10 S11 S7 S0S3S5 SlotEN

File: slot.kicad_sch Sheet: /Slot/ R. Veips

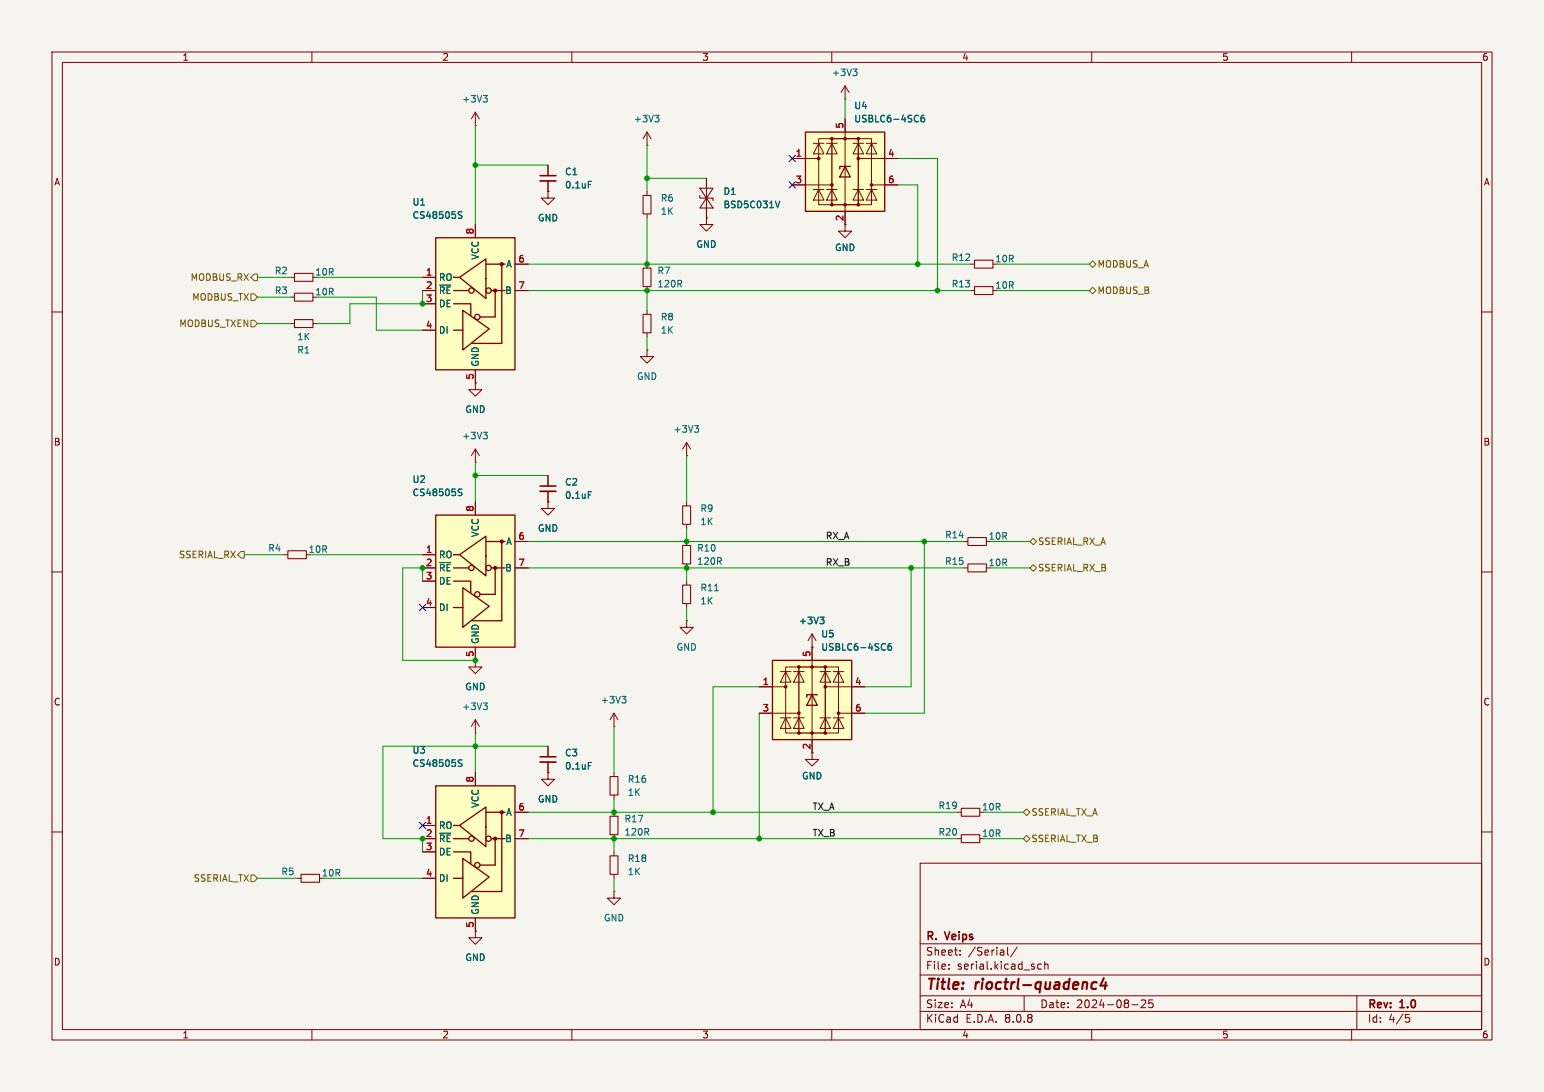
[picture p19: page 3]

File: serial.kicad_sch Sheet: /Serial/ R. Veips

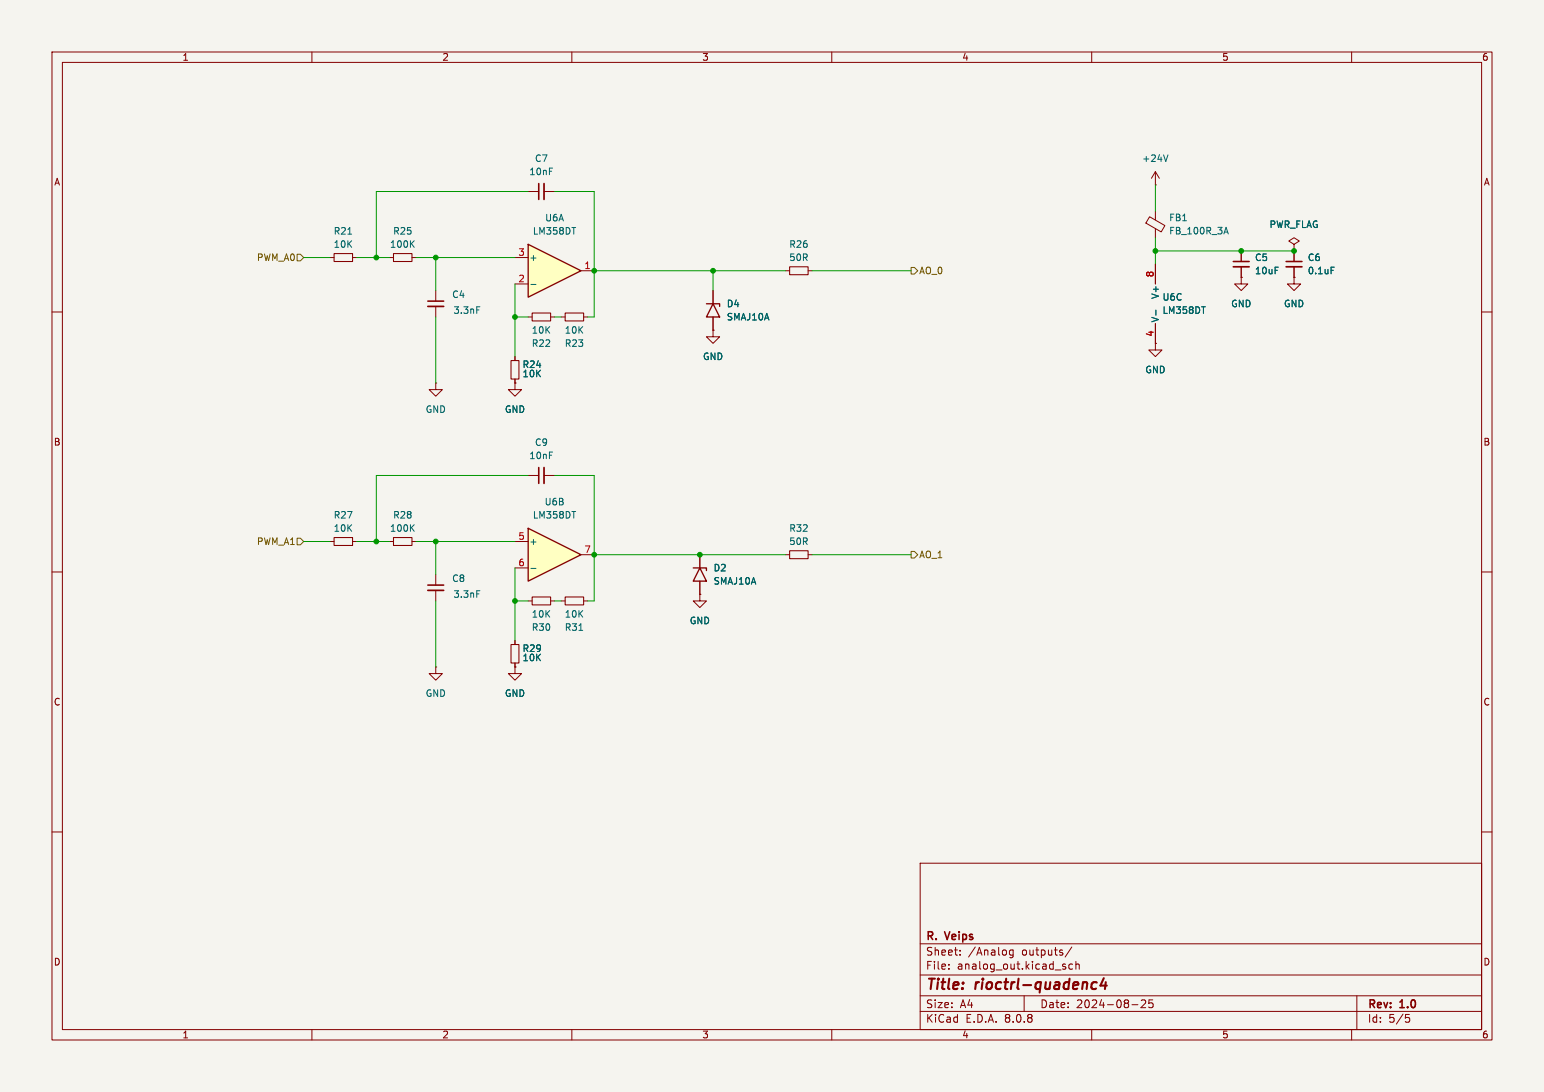
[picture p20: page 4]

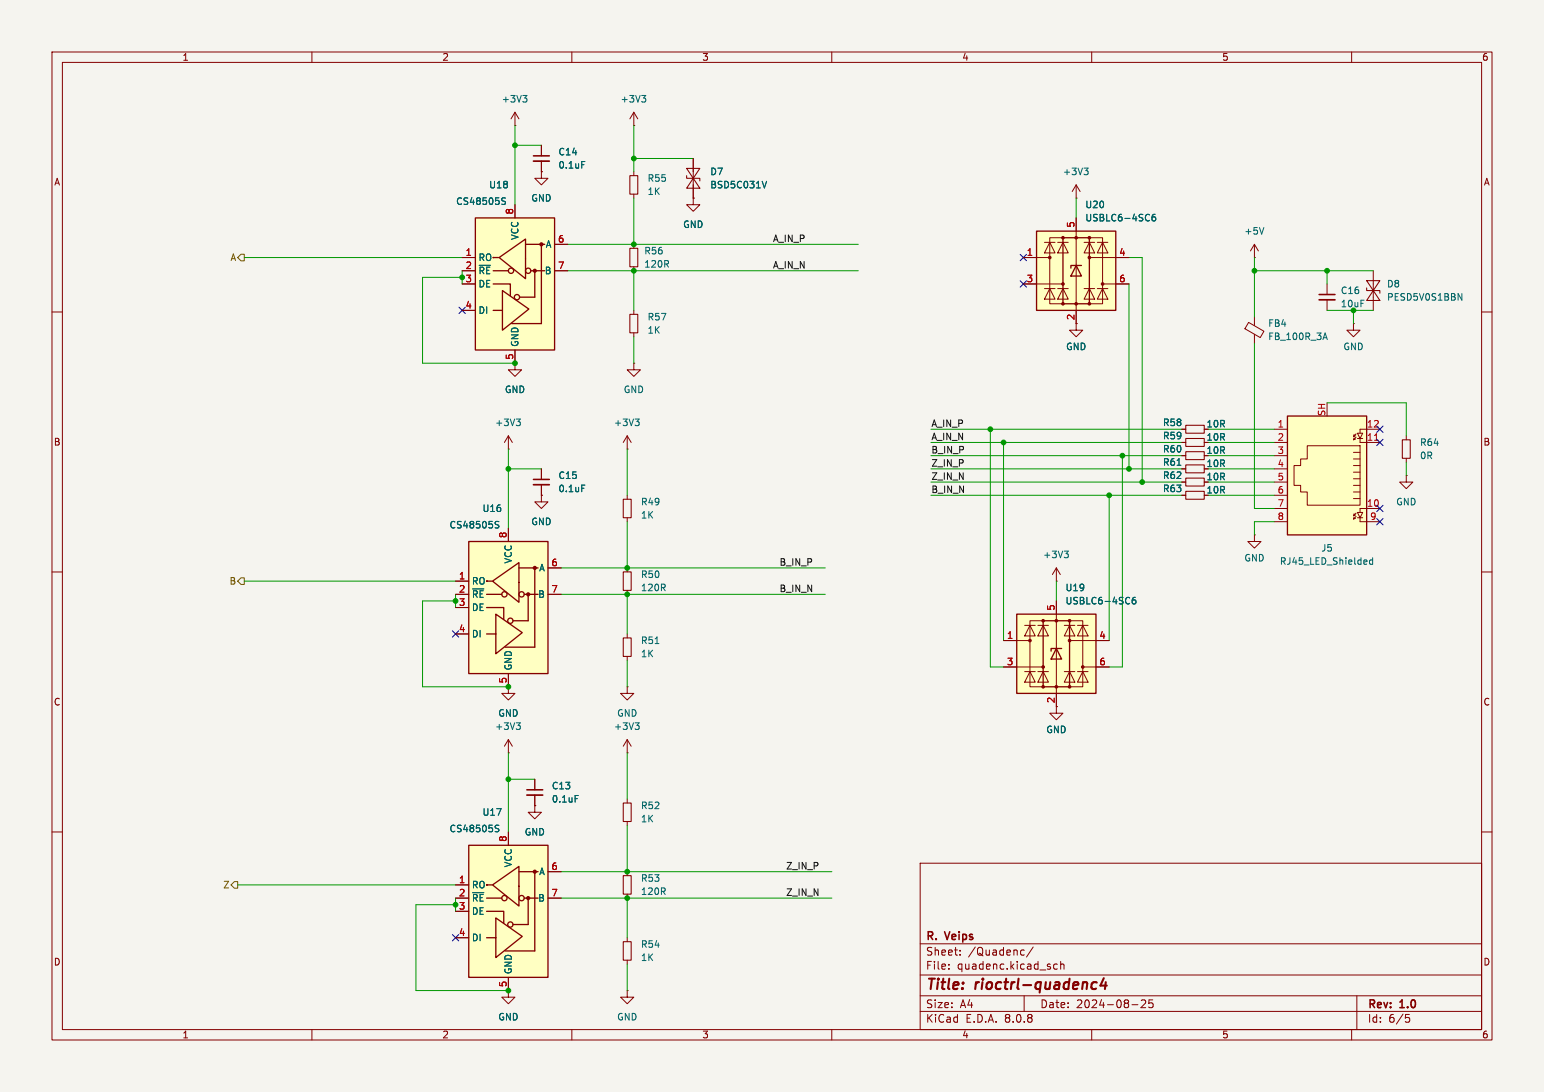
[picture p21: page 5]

0.1uF GND
D7BSD5C031V GND
GND GND

File: quadenc.kicad_sch Sheet: /Quadenc/ R. Veips

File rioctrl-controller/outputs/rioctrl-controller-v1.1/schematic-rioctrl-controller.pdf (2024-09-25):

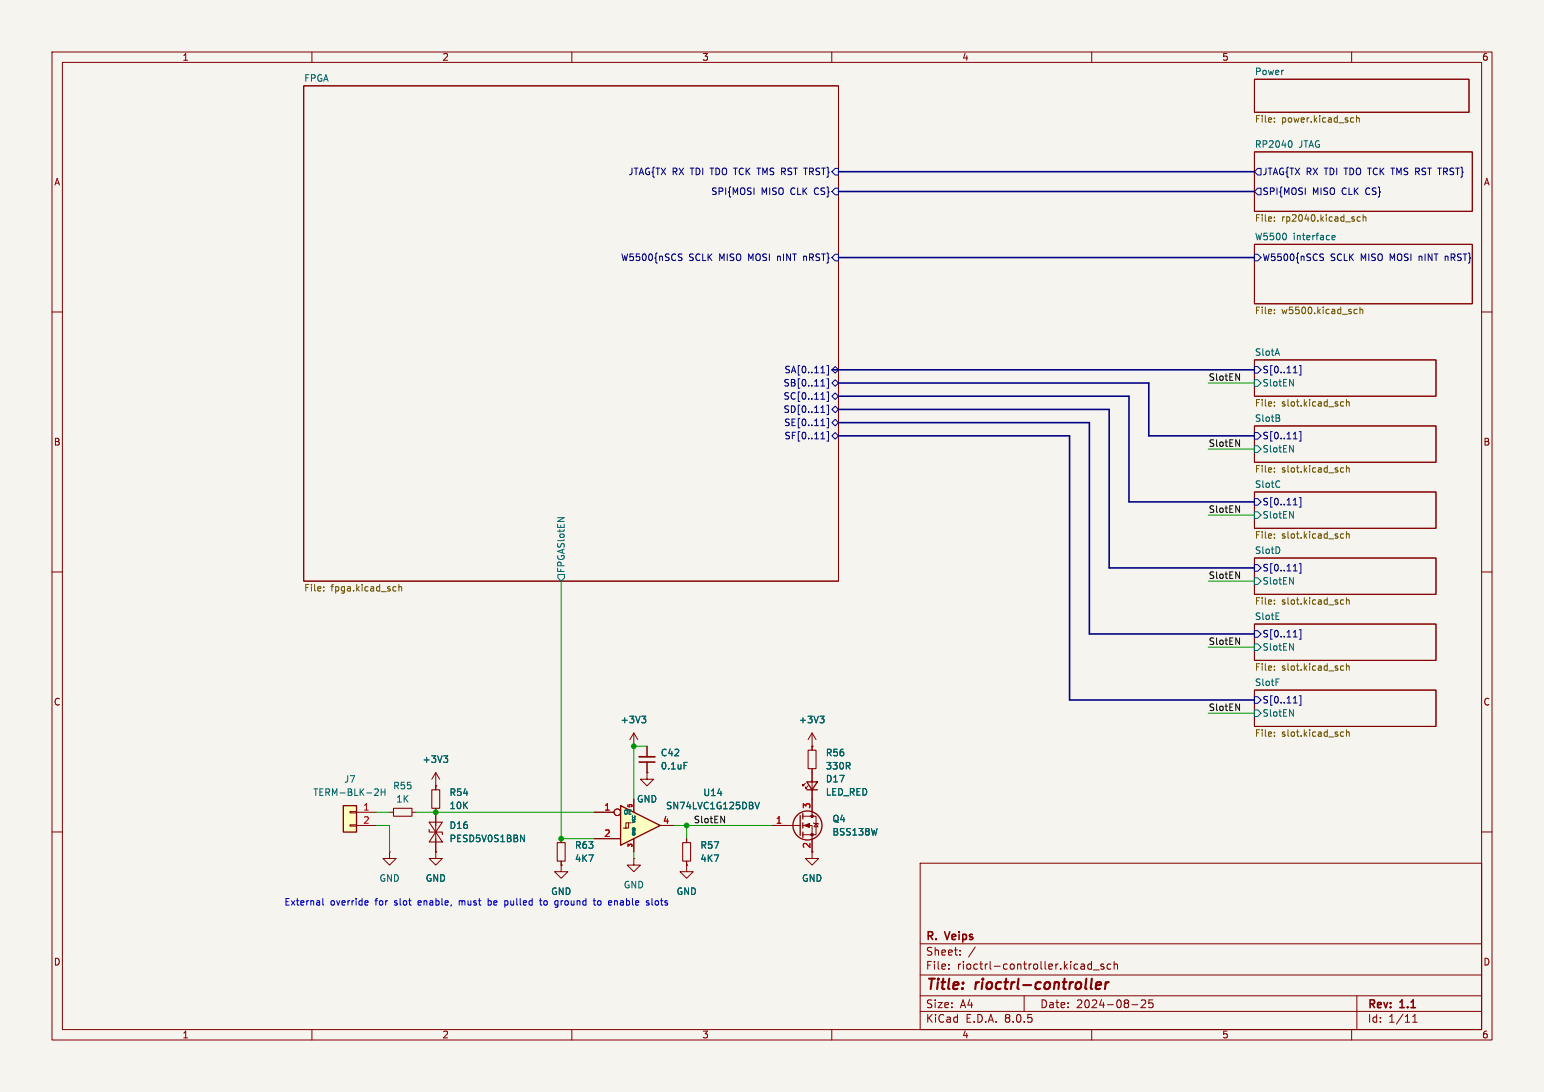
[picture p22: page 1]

File: slot.kicad_sch Power File: power.kicad_sch SlotEN

SPI{MOSI MISO CLK CS} RP2040 JTAG

JTAG{TX RX TDI TDO TCK TMS RST TRST}

SPI{MOSI MISO CLK CS} FPGASlotEN

W5500{nSCS SCLK MISO MOSI nINT nRST} W5500 interface File: w5500.kicad_sch SlotEN

W5500{nSCS SCLK MISO MOSI nINT nRST}

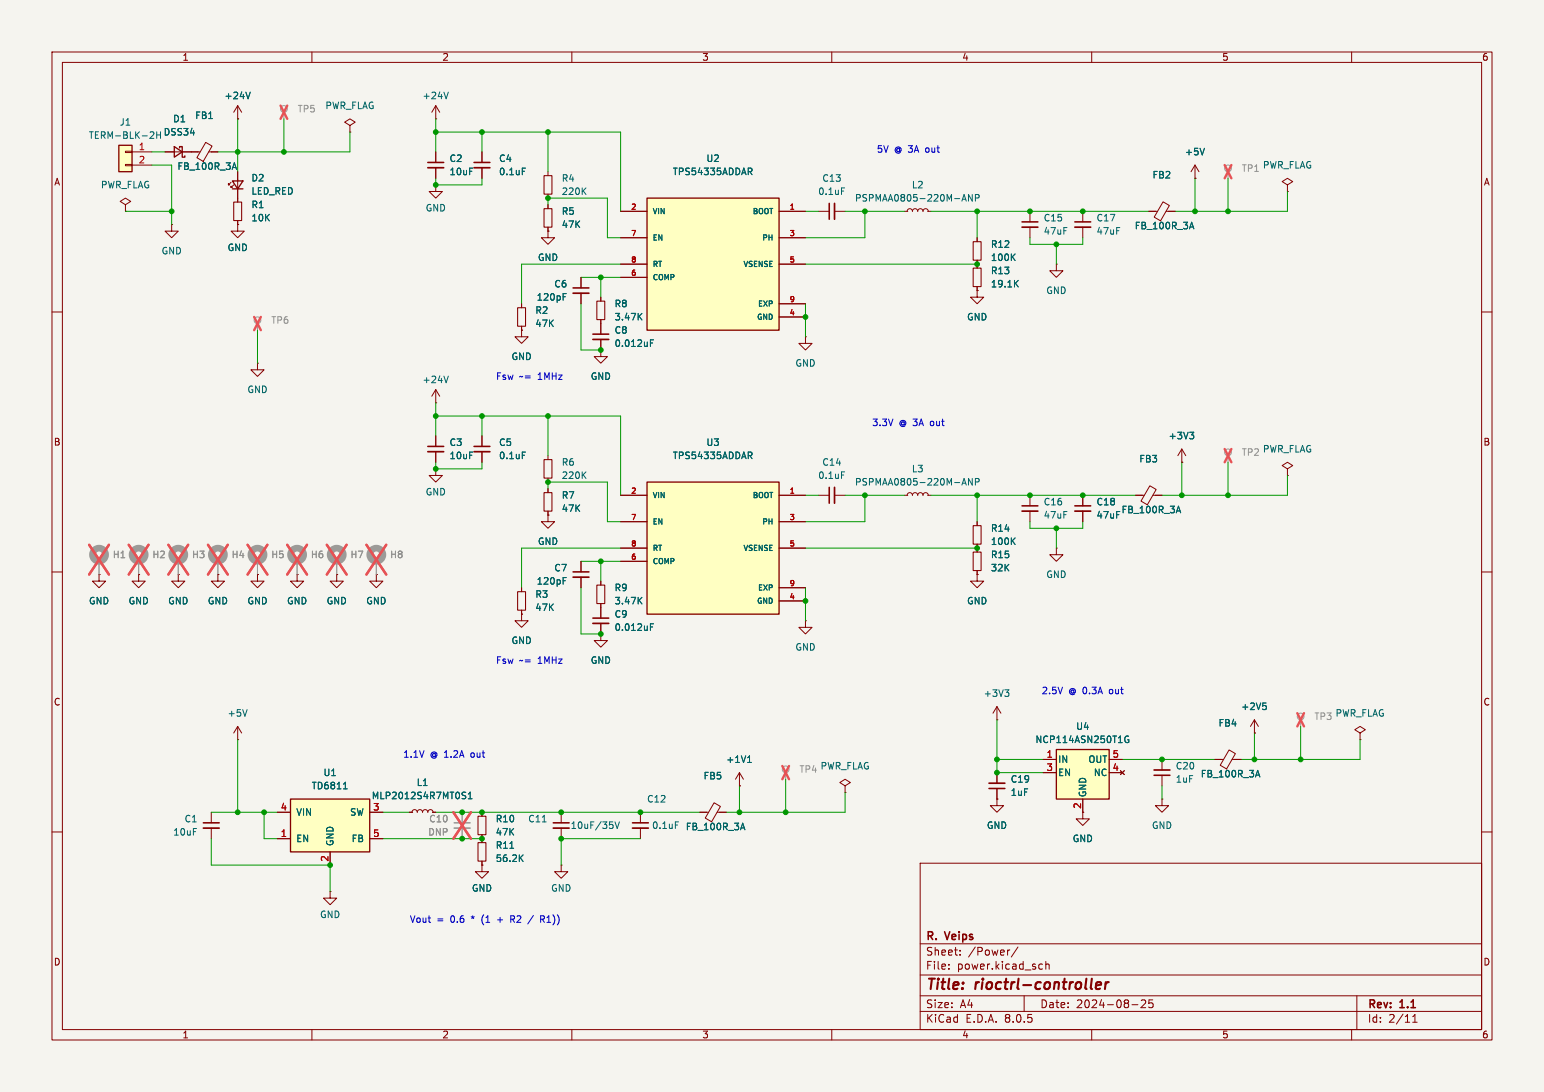
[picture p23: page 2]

2 EN 3 NC 4 OUT 5 GND GND

2 SW 3 VIN 4 FB 5 U1 TD6811 GND

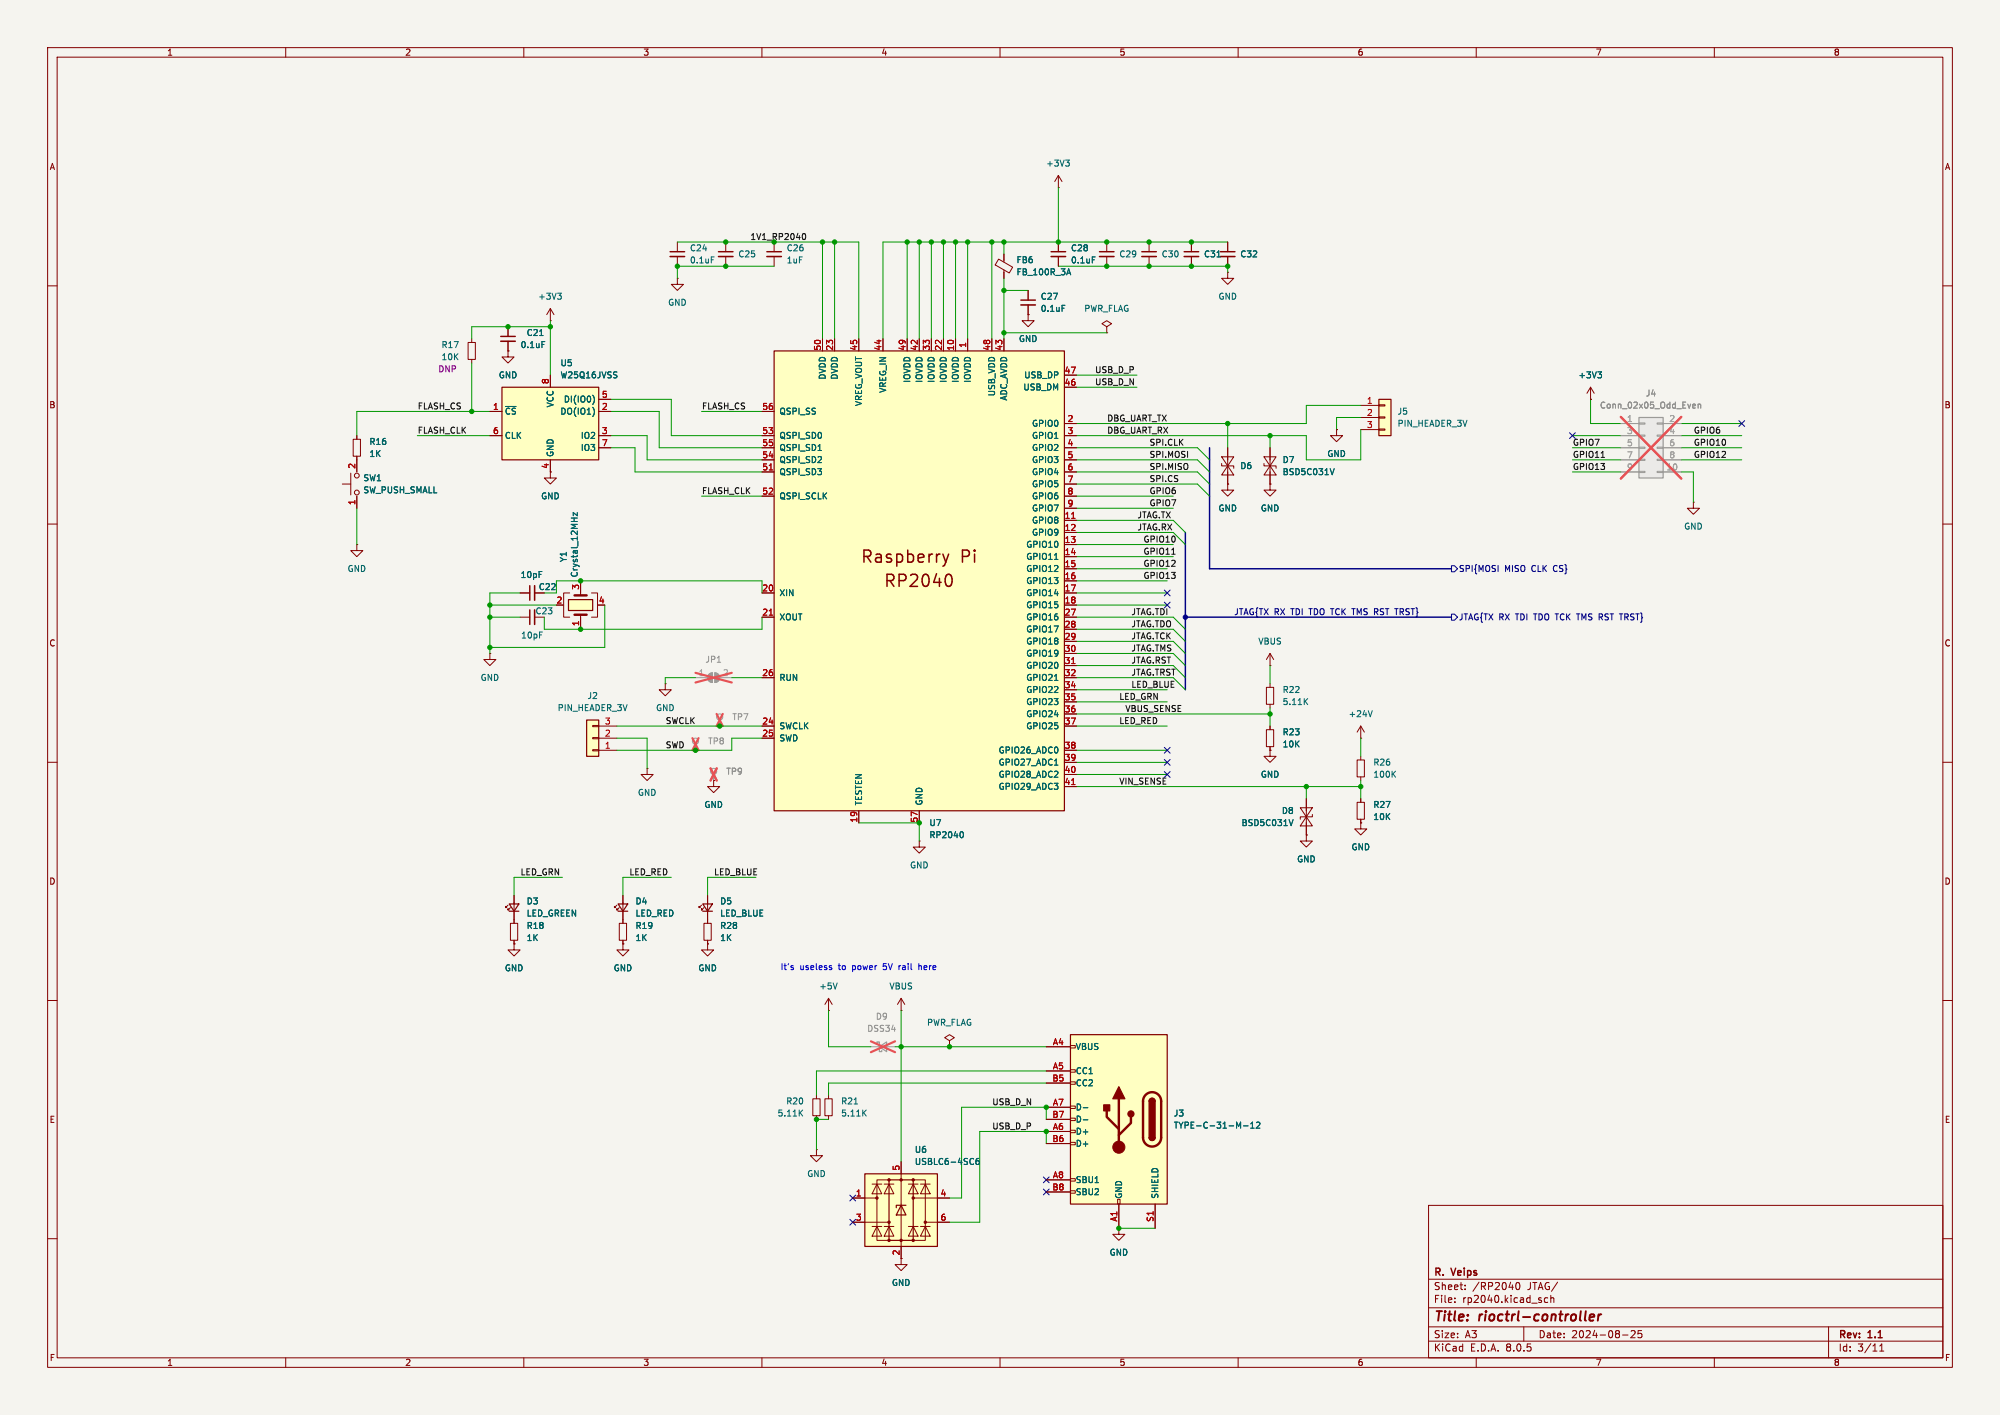
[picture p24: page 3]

1 IOVDD 10 GPIO8 11 GPIO9 12 GPIO10 13 GPIO11 14 GPIO12 15 GPIO13 16 GPIO14 17 GPIO15 18 TESTEN 19 GPIO0 2 XIN 20 XOUT 21 IOVDD 22 DVDD 23 SWCLK 24 SWD 25 RUN 26 GPIO16 27 GPIO17 28 GPIO18 29 GPIO1 3 GPIO19 30 GPIO20 31 GPIO21 32 IOVDD 33 GPIO22 34 GPIO23 35 GPIO24 36 GPIO25 37 GPIO26_ADC0 38 GPIO27_ADC1 39 GPIO2 4 GPIO28_ADC2 40 GPIO29_ADC3 41 IOVDD 42 ADC_AVDD 43 VREG_IN 44 VREG_VOUT 45 USB_DM 46 USB_DP 47 USB_VDD 48 IOVDD 49 GPIO3 5 DVDD 50 QSPI_SD3 51 QSPI_SCLK 52 QSPI_SD0 53 QSPI_SD2 54 QSPI_SD1 55 QSPI_SS 56 GND 57 GPIO4 6 GPIO5 7 GPIO6 8 GPIO7 9 FB6 FB_100R_3A C27

1 IOVDD 10 GPIO8 11 GPIO9 12 GPIO10 13 GPIO11 14 GPIO12 15 GPIO13 16 GPIO14 17 GPIO15 18 TESTEN 19 GPIO0 2 XIN 20 XOUT 21 IOVDD 22 DVDD 23 SWCLK 24 SWD 25 RUN 26 GPIO16 27 GPIO17 28 GPIO18 29 GPIO1 3 GPIO19 30 GPIO20 31 GPIO21 32 IOVDD 33 GPIO22 34 GPIO23 35 GPIO24 36 GPIO25 37 GPIO26_ADC0 38 GPIO27_ADC1 39 GPIO2 4 GPIO28_ADC2 40 GPIO29_ADC3 41 IOVDD 42 ADC_AVDD 43 VREG_IN 44 VREG_VOUT 45 USB_DM 46 USB_DP 47 USB_VDD 48 IOVDD 49 GPIO3 5 DVDD 50 QSPI_SD3 51 QSPI_SCLK 52 QSPI_SD0 53 QSPI_SD2 54 QSPI_SD1 55 QSPI_SS 56 GND 57 GPIO4 6 GPIO5 7 GPIO6 8 GPIO7 9 U7 RP2040 TP9 GND GND GND

DBG_UART_RX USB_D_P
SPI{MOSI MISO CLK CS} DBG_UART_TX USB_D_N

JTAG{TX RX TDI TDO TCK TMS RST TRST}

It's useless to power 5V rail here

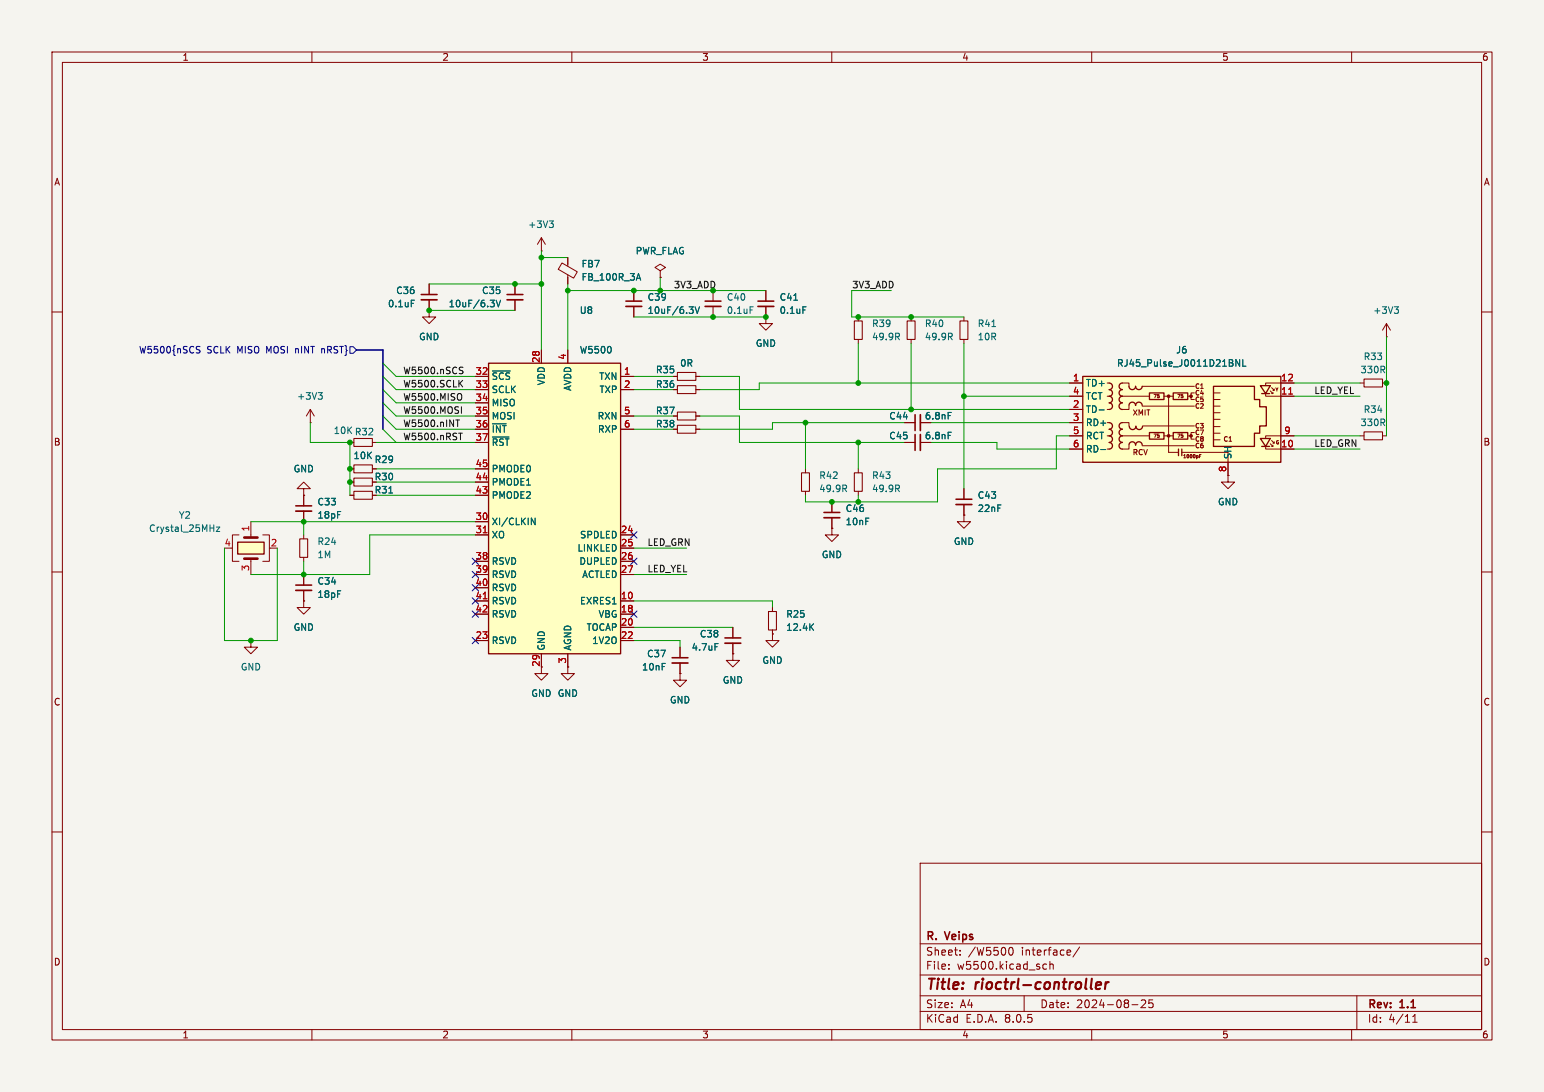
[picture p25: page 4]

4 RSVD 40 RSVD 41 RSVD 42 PMODE2 43 PMODE1 44 PMODE0 45 RXN 5 RXP 6 C39

4 RSVD 40 RSVD 41 RSVD 42 PMODE2 43 PMODE1 44 PMODE0 45 RXN 5 RXP 6 U8 W5500 C37

3 XI/CLKIN 30 XO 31 ~{SCS} 32 SCLK 33 MISO 34 MOSI 35 ~{INT} 36 ~{RST} 37 RSVD 38 RSVD 39 AVDD

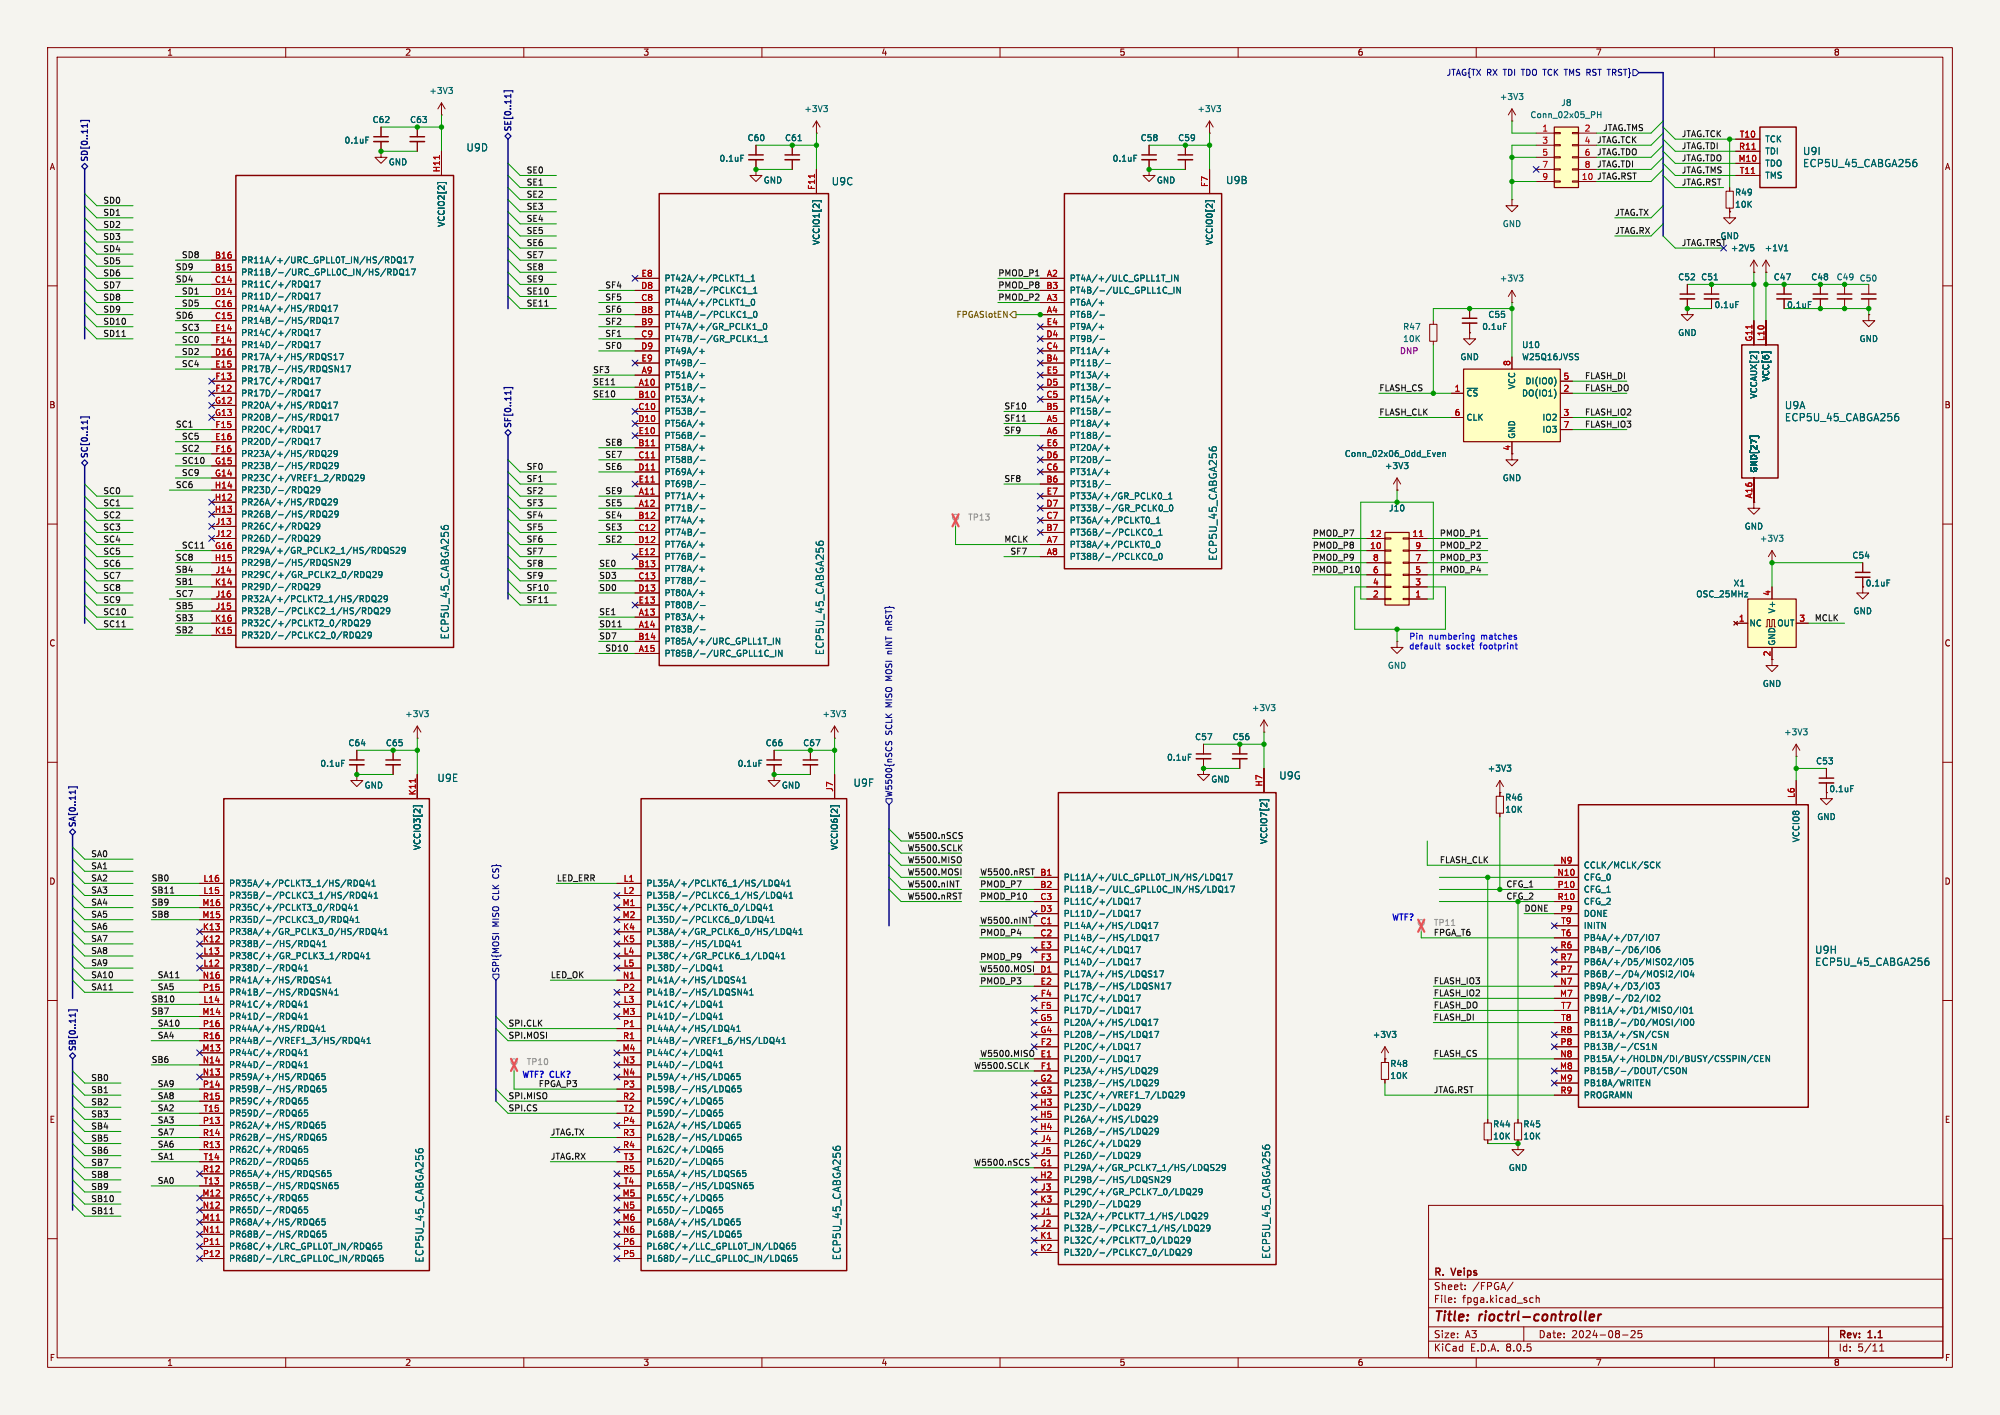
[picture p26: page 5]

JTAG{TX RX TDI TDO TCK TMS RST TRST}
0.1uFR49

JTAG.TMS
JTAG.TCK
JTAG.TDI JTAG.TRST
JTAG.TDO

8 U10 W25Q16JVSS VCCIO6[2] J7 PL38A/+/GR_PCLK6_0/HS/LDQ41 K4 PL38B/-/HS/LDQ41 K5 PL35A/+/PCLKT6_1/HS/LDQ41 L1 PL35B/-/PCLKC6_1/HS/LDQ41 L2 PL41C/+/LDQ41 L3 PL38C/+/GR_PCLK6_1/LDQ41 L4 PL38D/-/LDQ41 L5 PL35C/+/PCLKT6_0/LDQ41 M1 PL35D/-/PCLKC6_0/LDQ41 M2 PL41D/-/LDQ41 M3 PL44C/+/LDQ41 M4 PL65C/+/LDQ65 M5 PL68A/+/HS/LDQ65 M6 PL41A/+/HS/LDQS41 N1 PL44D/-/LDQ41 N3 PL59A/+/HS/LDQ65 N4 PL65D/-/LDQ65 N5 PL68B/-/HS/LDQ65 N6 PL44A/+/HS/LDQ41 P1 PL41B/-/HS/LDQSN41 P2 PL59B/-/HS/LDQ65 P3 PL62A/+/HS/LDQ65 P4 PL68D/-/LLC_GPLL0C_IN/LDQ65 P5 PL68C/+/LLC_GPLL0T_IN/LDQ65 P6 PL44B/-/VREF1_6/HS/LDQ41 R1 PL59C/+/LDQ65 R2 PL62B/-/HS/LDQ65 R3 PL62C/+/LDQ65 R4 PL65A/+/HS/LDQS65 R5 PL59D/-/LDQ65 T2 PL62D/-/LDQ65 T3 PL65B/-/HS/LDQSN65 T4 U9F ECP5U_45_CABGA256 GND

Id: 5/11 Title: rioctrl-controller File: fpga.kicad_sch Sheet: /FPGA/ R. Veips

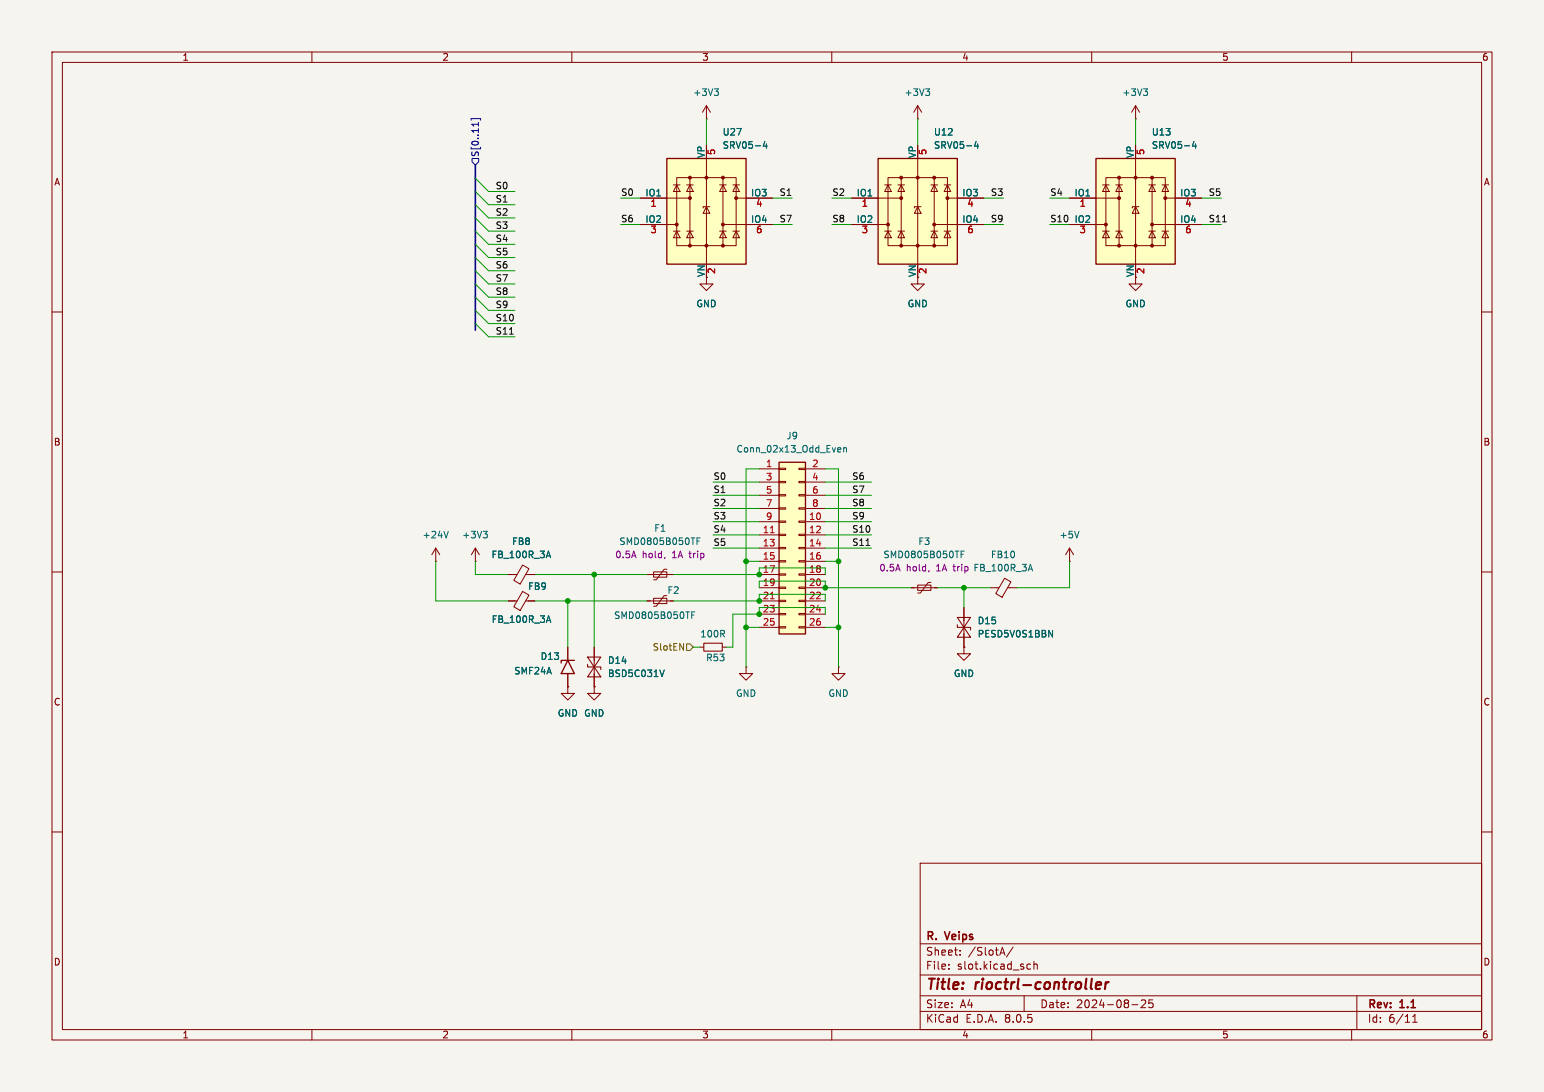
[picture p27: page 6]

Id: 6/11 Title: rioctrl-controller File: slot.kicad_sch Sheet: /SlotA/ R. Veips

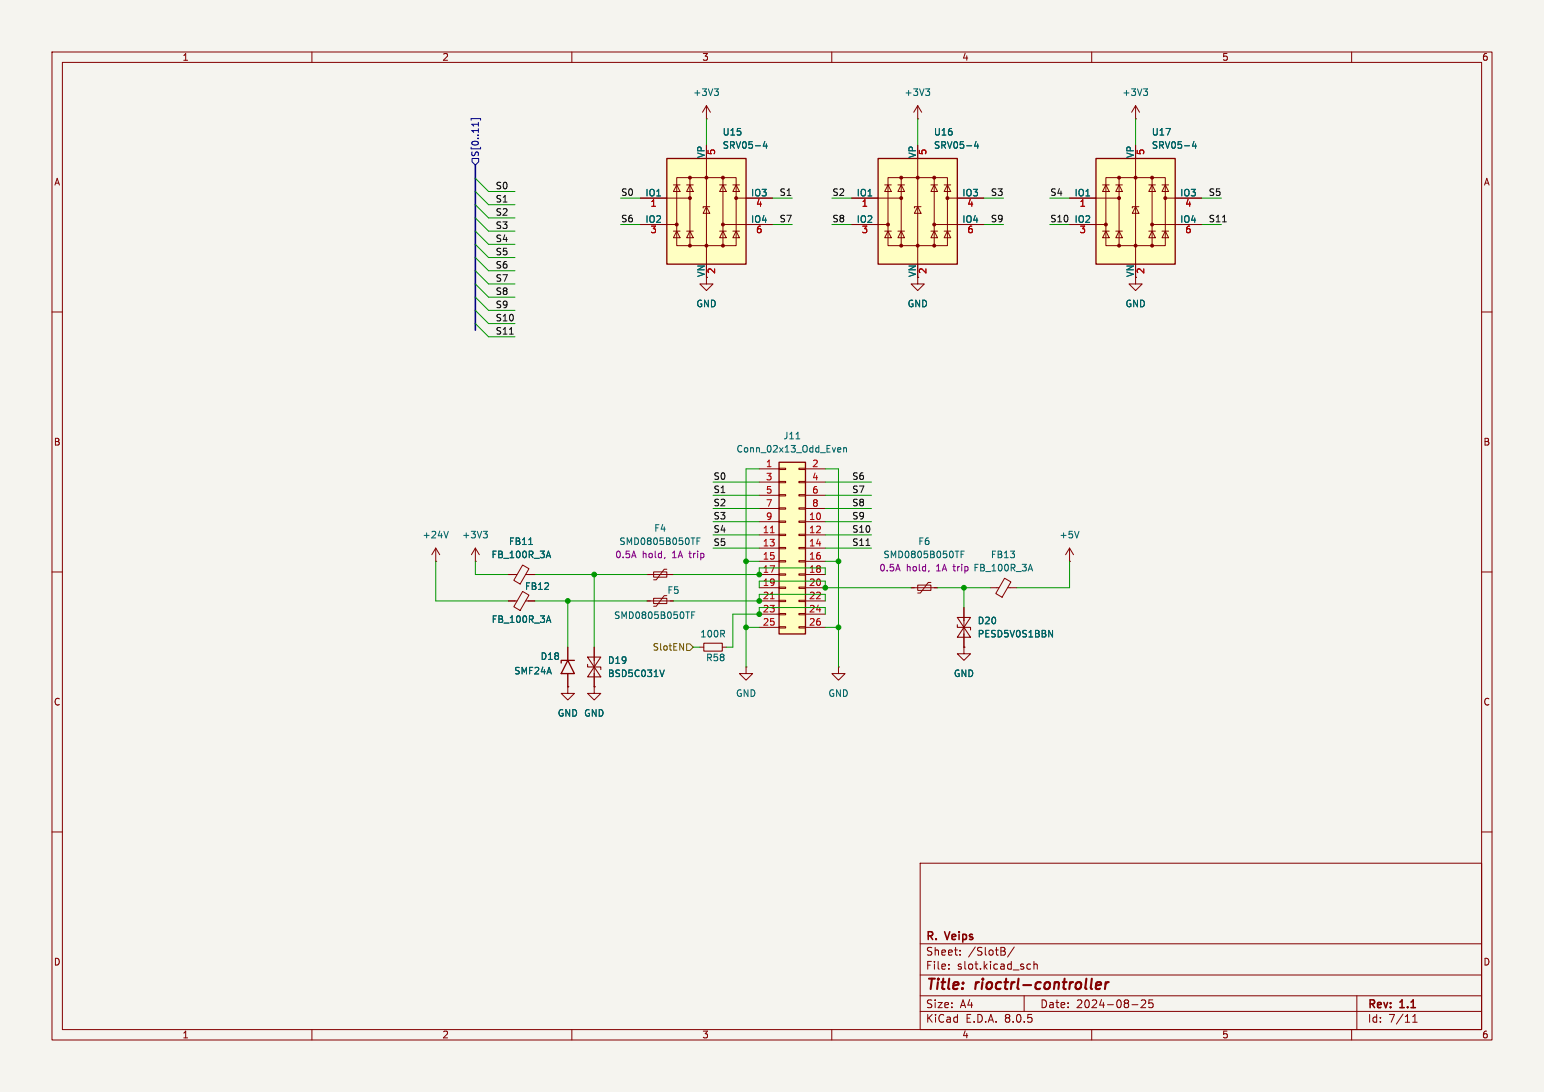
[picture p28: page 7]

Id: 7/11 Title: rioctrl-controller File: slot.kicad_sch Sheet: /SlotB/ R. Veips D20 PESD5V0S1BBN GND


Id: 8/11 Title: rioctrl-controller File: slot.kicad_sch Sheet: /SlotC/ R. Veips GND GND


Id: 9/11 Title: rioctrl-controller File: slot.kicad_sch Sheet: /SlotD/ R. Veips


Id: 10/11 Title: rioctrl-controller File: slot.kicad_sch Sheet: /SlotE/ R. Veips D29 PESD5V0S1BBN GND


Id: 11/11 Title: rioctrl-controller File: slot.kicad_sch Sheet: /SlotF/ R. Veips GND GND

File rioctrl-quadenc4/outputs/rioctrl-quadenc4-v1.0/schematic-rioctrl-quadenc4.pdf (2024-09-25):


File: rioctrl-quadenc4.kicad_sch Sheet: / R. Veips ZAB Quadenc File: quadenc.kicad_sch ZAB Quadenc1 File: quadenc.kicad_sch ZAB Quadenc3 File: quadenc.kicad_sch ZAB Quadenc2 File: quadenc.kicad_sch S0S4S1S5S2S3S6S8S7S9 S11 S10 SlotEN



3 5 7 9 11 13 15 | 4 6 8 10 12 14 16 | S6S8S9S10 S11 S7 S0S3S5 SlotEN

File: slot.kicad_sch Sheet: /Slot/ R. Veips




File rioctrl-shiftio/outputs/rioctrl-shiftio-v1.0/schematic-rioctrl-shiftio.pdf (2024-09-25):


S11 S10 ~{SlotEN} S6S7S9S8S0S1S4S5S3S2 Slot File: slot.kicad_sch

~{OE} DATA_IN Output shiftreg File: out_shiftreg.kicad_sch SlotEN

Input shiftreg File: input_shiftreg.kicad_sch CLOCK
LOAD

Id: 1/28 Title: File: rioctrl-shiftio.kicad_sch Sheet: /


Id: 2/28 Title: File: slot.kicad_sch Sheet: /Slot/ GND


Digital output File: digital_output.kicad_sch COLLECTOR
COLLECTOR






Digital output File: digital_output.kicad_sch COLLECTOR
COLLECTOR





Digital output File: digital_output.kicad_sch COLLECTOR
COLLECTOR





Digital output File: digital_output.kicad_sch COLLECTOR
COLLECTOR









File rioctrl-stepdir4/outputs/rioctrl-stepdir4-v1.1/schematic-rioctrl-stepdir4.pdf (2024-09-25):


Step dir output 4 File: stepdir.kicad_sch
Step dir output 3 File: stepdir.kicad_sch STEP
DIR

Step dir output 2 File: stepdir.kicad_sch S0S1S2S3S4 SlotEN

Step dir output 1 File: stepdir.kicad_sch STEP

File: rioctrl-stepdir4.kicad_sch Sheet: / R. Veips STEP


+24V rail when slot enable is high PWR_FLAG

3 5 7 9 11 13 15 | 4 6 8 10 12 14 16 | S10 S9S8S7 SlotEN


8 U2 CS48505S RO 1 ~{RE} 2 DE 3 DI 4 GND



8 U8 CS48505S RO 1 ~{RE} 2 DE 3 DI 4 GND


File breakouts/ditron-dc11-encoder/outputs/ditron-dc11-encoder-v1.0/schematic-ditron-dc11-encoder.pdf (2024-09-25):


Id: 1/1 Title: File: ditron-dc11-encoder.kicad_sch Sheet: / PWR_FLAG

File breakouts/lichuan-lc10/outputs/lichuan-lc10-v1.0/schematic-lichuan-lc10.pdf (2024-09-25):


Digital outputs are NPN
ENC_Z_P DO_FAULT ENC_Z_N

Id: 1/1 Title: File: lichuan-lc10.kicad_sch Sheet: / PWR_FLAG

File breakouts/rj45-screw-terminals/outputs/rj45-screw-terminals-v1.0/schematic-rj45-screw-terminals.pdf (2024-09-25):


Id: 1/1 Title: File: rj45-screw-terminals.kicad_sch Sheet: /

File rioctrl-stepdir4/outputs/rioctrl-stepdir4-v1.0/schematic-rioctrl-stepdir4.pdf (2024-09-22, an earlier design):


Step dir output 4 File: stepdir.kicad_sch
Step dir output 3 File: stepdir.kicad_sch STEP
DIR

Step dir output 2 File: stepdir.kicad_sch S0S1S2S3S4 SlotEN

Step dir output 1 File: stepdir.kicad_sch STEP

File: rioctrl-stepdir4.kicad_sch Sheet: / R. Veips STEP


+24V rail when slot enable is high PWR_FLAG

3 5 7 9 11 13 15 | 4 6 8 10 12 14 16 | S10 S9S8S7 SlotEN


8 U2 CS48505S RO 1 ~{RE} 2 DE 3 DI 4 GND



8 U8 CS48505S RO 1 ~{RE} 2 DE 3 DI 4 GND


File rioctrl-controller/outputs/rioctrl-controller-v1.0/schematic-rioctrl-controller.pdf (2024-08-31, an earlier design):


File: slot.kicad_sch Power File: power.kicad_sch SlotEN

SPI{MOSI MISO CLK CS} RP2040 JTAG

JTAG{TX RX TDI TDO TCK TMS RST TRST}

SPI{MOSI MISO CLK CS} FPGASlotEN

W5500{nSCS SCLK MISO MOSI nINT nRST} W5500 interface File: w5500.kicad_sch SlotEN

W5500{nSCS SCLK MISO MOSI nINT nRST}


2 EN 3 NC 4 OUT 5 GND GND

2 SW 3 VIN 4 FB 5 U1 TD6811 GND


1 IOVDD 10 GPIO8 11 GPIO9 12 GPIO10 13 GPIO11 14 GPIO12 15 GPIO13 16 GPIO14 17 GPIO15 18 TESTEN 19 GPIO0 2 XIN 20 XOUT 21 IOVDD 22 DVDD 23 SWCLK 24 SWD 25 RUN 26 GPIO16 27 GPIO17 28 GPIO18 29 GPIO1 3 GPIO19 30 GPIO20 31 GPIO21 32 IOVDD 33 GPIO22 34 GPIO23 35 GPIO24 36 GPIO25 37 GPIO26_ADC0 38 GPIO27_ADC1 39 GPIO2 4 GPIO28_ADC2 40 GPIO29_ADC3 41 IOVDD 42 ADC_AVDD 43 VREG_IN 44 VREG_VOUT 45 USB_DM 46 USB_DP 47 USB_VDD 48 IOVDD 49 GPIO3 5 DVDD 50 QSPI_SD3 51 QSPI_SCLK 52 QSPI_SD0 53 QSPI_SD2 54 QSPI_SD1 55 QSPI_SS 56 GND 57 GPIO4 6 GPIO5 7 GPIO6 8 GPIO7 9 Y1

1 IOVDD 10 GPIO8 11 GPIO9 12 GPIO10 13 GPIO11 14 GPIO12 15 GPIO13 16 GPIO14 17 GPIO15 18 TESTEN 19 GPIO0 2 XIN 20 XOUT 21 IOVDD 22 DVDD 23 SWCLK 24 SWD 25 RUN 26 GPIO16 27 GPIO17 28 GPIO18 29 GPIO1 3 GPIO19 30 GPIO20 31 GPIO21 32 IOVDD 33 GPIO22 34 GPIO23 35 GPIO24 36 GPIO25 37 GPIO26_ADC0 38 GPIO27_ADC1 39 GPIO2 4 GPIO28_ADC2 40 GPIO29_ADC3 41 IOVDD 42 ADC_AVDD 43 VREG_IN 44 VREG_VOUT 45 USB_DM 46 USB_DP 47 USB_VDD 48 IOVDD 49 GPIO3 5 DVDD 50 QSPI_SD3 51 QSPI_SCLK 52 QSPI_SD0 53 QSPI_SD2 54 QSPI_SD1 55 QSPI_SS 56 GND 57 GPIO4 6 GPIO5 7 GPIO6 8 GPIO7 9 U7 RP2040

JTAG{TX RX TDI TDO TCK TMS RST TRST} SPI.CLK
SPI.MISO
SPI.CS
LED_REDGPIO6

SPI{MOSI MISO CLK CS} SWD

JTAG{TX RX TDI TDO TCK TMS RST TRST}


4 RSVD 40 RSVD 41 RSVD 42 PMODE2 43 PMODE1 44 PMODE0 45 RXN 5 RXP 6 C39

4 RSVD 40 RSVD 41 RSVD 42 PMODE2 43 PMODE1 44 PMODE0 45 RXN 5 RXP 6 U8 W5500 C37

3 XI/CLKIN 30 XO 31 ~{SCS} 32 SCLK 33 MISO 34 MOSI 35 ~{INT} 36 ~{RST} 37 RSVD 38 RSVD 39 AVDD


JTAG{TX RX TDI TDO TCK TMS RST TRST}
0.1uFR49

JTAG.TMS
JTAG.TCK
JTAG.TDI JTAG.TRST
JTAG.TDO

8 U10 W25Q16JVSS VCCIO6[2] J7 PL38A/+/GR_PCLK6_0/HS/LDQ41 K4 PL38B/-/HS/LDQ41 K5 PL35A/+/PCLKT6_1/HS/LDQ41 L1 PL35B/-/PCLKC6_1/HS/LDQ41 L2 PL41C/+/LDQ41 L3 PL38C/+/GR_PCLK6_1/LDQ41 L4 PL38D/-/LDQ41 L5 PL35C/+/PCLKT6_0/LDQ41 M1 PL35D/-/PCLKC6_0/LDQ41 M2 PL41D/-/LDQ41 M3 PL44C/+/LDQ41 M4 PL65C/+/LDQ65 M5 PL68A/+/HS/LDQ65 M6 PL41A/+/HS/LDQS41 N1 PL44D/-/LDQ41 N3 PL59A/+/HS/LDQ65 N4 PL65D/-/LDQ65 N5 PL68B/-/HS/LDQ65 N6 PL44A/+/HS/LDQ41 P1 PL41B/-/HS/LDQSN41 P2 PL59B/-/HS/LDQ65 P3 PL62A/+/HS/LDQ65 P4 PL68D/-/LLC_GPLL0C_IN/LDQ65 P5 PL68C/+/LLC_GPLL0T_IN/LDQ65 P6 PL44B/-/VREF1_6/HS/LDQ41 R1 PL59C/+/LDQ65 R2 PL62B/-/HS/LDQ65 R3 PL62C/+/LDQ65 R4 PL65A/+/HS/LDQS65 R5 PL59D/-/LDQ65 T2 PL62D/-/LDQ65 T3 PL65B/-/HS/LDQSN65 T4 U9F ECP5U_45_CABGA256 GND

Id: 5/11 Title: rioctrl-controller File: fpga.kicad_sch Sheet: /FPGA/ R. Veips


Id: 6/11 Title: rioctrl-controller File: slot.kicad_sch Sheet: /SlotA/ R. Veips


Id: 7/11 Title: rioctrl-controller File: slot.kicad_sch Sheet: /SlotB/ R. Veips D20 PESD5V0S1BBN GND


Id: 8/11 Title: rioctrl-controller File: slot.kicad_sch Sheet: /SlotC/ R. Veips GND GND


Id: 9/11 Title: rioctrl-controller File: slot.kicad_sch Sheet: /SlotD/ R. Veips


Id: 10/11 Title: rioctrl-controller File: slot.kicad_sch Sheet: /SlotE/ R. Veips D29 PESD5V0S1BBN GND


Id: 11/11 Title: rioctrl-controller File: slot.kicad_sch Sheet: /SlotF/ R. Veips GND GND

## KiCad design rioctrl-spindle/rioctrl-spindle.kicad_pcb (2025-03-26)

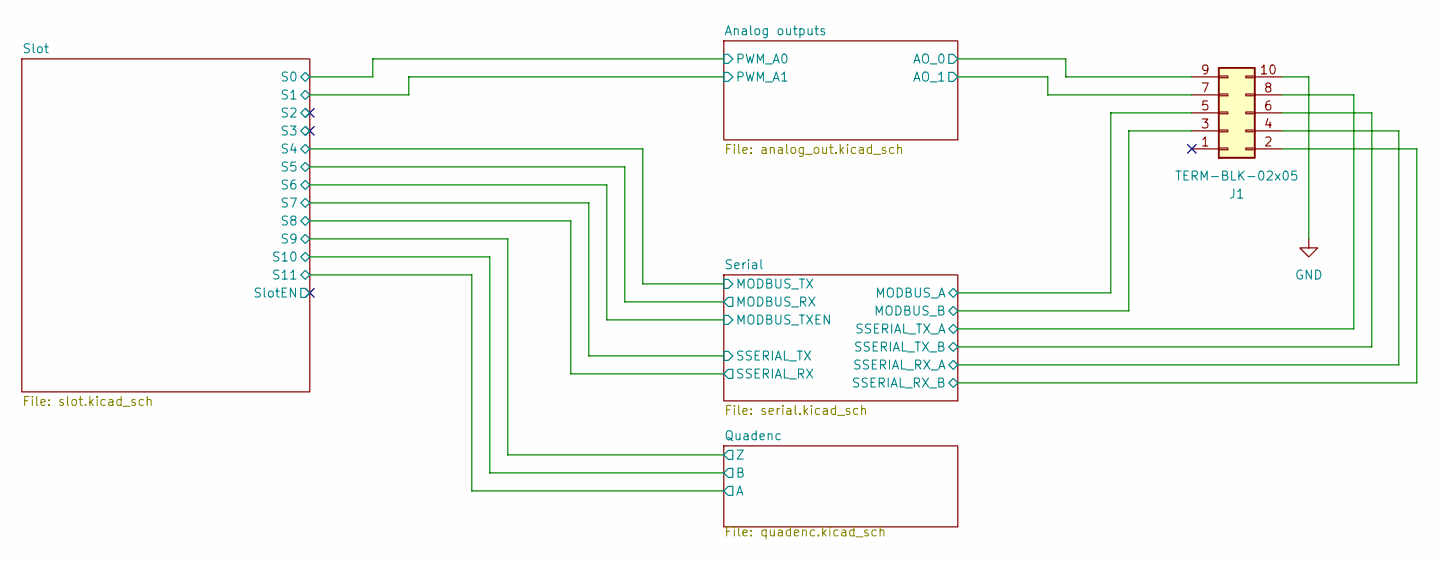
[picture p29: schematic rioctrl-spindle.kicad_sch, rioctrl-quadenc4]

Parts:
J1: TERM-BLK-02x05; JL15EDGRHC-35005B02; MPN JL15EDGRHC-35005B02; LCSC# C2908411

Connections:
/Analog outputs/AO_0: J1.9; also elsewhere on the board
/Analog outputs/AO_1: J1.7; also elsewhere on the board
/Serial/MODBUS_A: J1.5; also elsewhere on the board
/Serial/MODBUS_B: J1.3; also elsewhere on the board
/Serial/SSERIAL_RX_A: J1.4; also elsewhere on the board
/Serial/SSERIAL_RX_B: J1.2; also elsewhere on the board
/Serial/SSERIAL_TX_A: J1.8; also elsewhere on the board
/Serial/SSERIAL_TX_B: J1.6; also elsewhere on the board
GND: J1.10; also elsewhere on the board

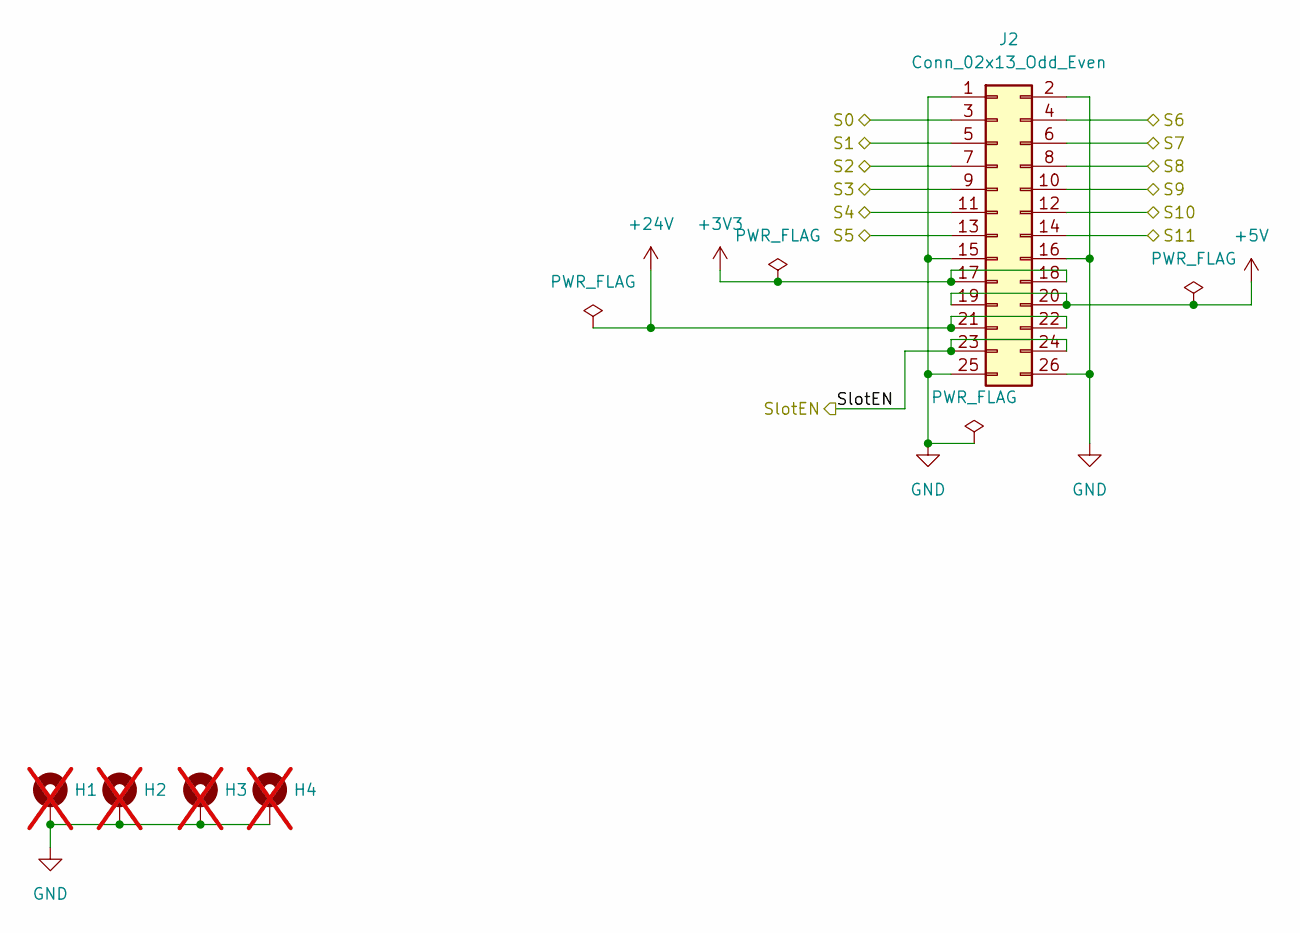
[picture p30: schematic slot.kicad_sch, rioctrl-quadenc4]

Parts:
H1, H2, H3, H4: MH_3.2mm; MountingHole_3.2mm_M3_Pad_Via; not fitted
J2: Conn_02x13_Odd_Even; PinHeader_2x13_P2.54mm_Horizontal; LCSC# C2894993

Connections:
+3V3: J2.17, J2.18; also elsewhere on the board
+5V: J2.19, J2.20; also elsewhere on the board
+24V: J2.21, J2.22; also elsewhere on the board
/Analog outputs/PWM_A0: J2.3; also elsewhere on the board
/Analog outputs/PWM_A1: J2.5; also elsewhere on the board
/Quadenc/A: J2.14; also elsewhere on the board
/Quadenc/B: J2.12; also elsewhere on the board
/Quadenc/Z: J2.10; also elsewhere on the board
/Serial/MODBUS_RX: J2.13; also elsewhere on the board
/Serial/MODBUS_TX: J2.11; also elsewhere on the board
/Serial/MODBUS_TXEN: J2.4; also elsewhere on the board
/Serial/SSERIAL_RX: J2.8; also elsewhere on the board
/Serial/SSERIAL_TX: J2.6; also elsewhere on the board
/Slot/S2: J2.7
/Slot/S3: J2.9
/Slot/SlotEN: J2.23, J2.24
GND: H1.1, H2.1, H3.1, H4.1, J2.1, J2.2, J2.15, J2.16, J2.25, J2.26; also elsewhere on the board

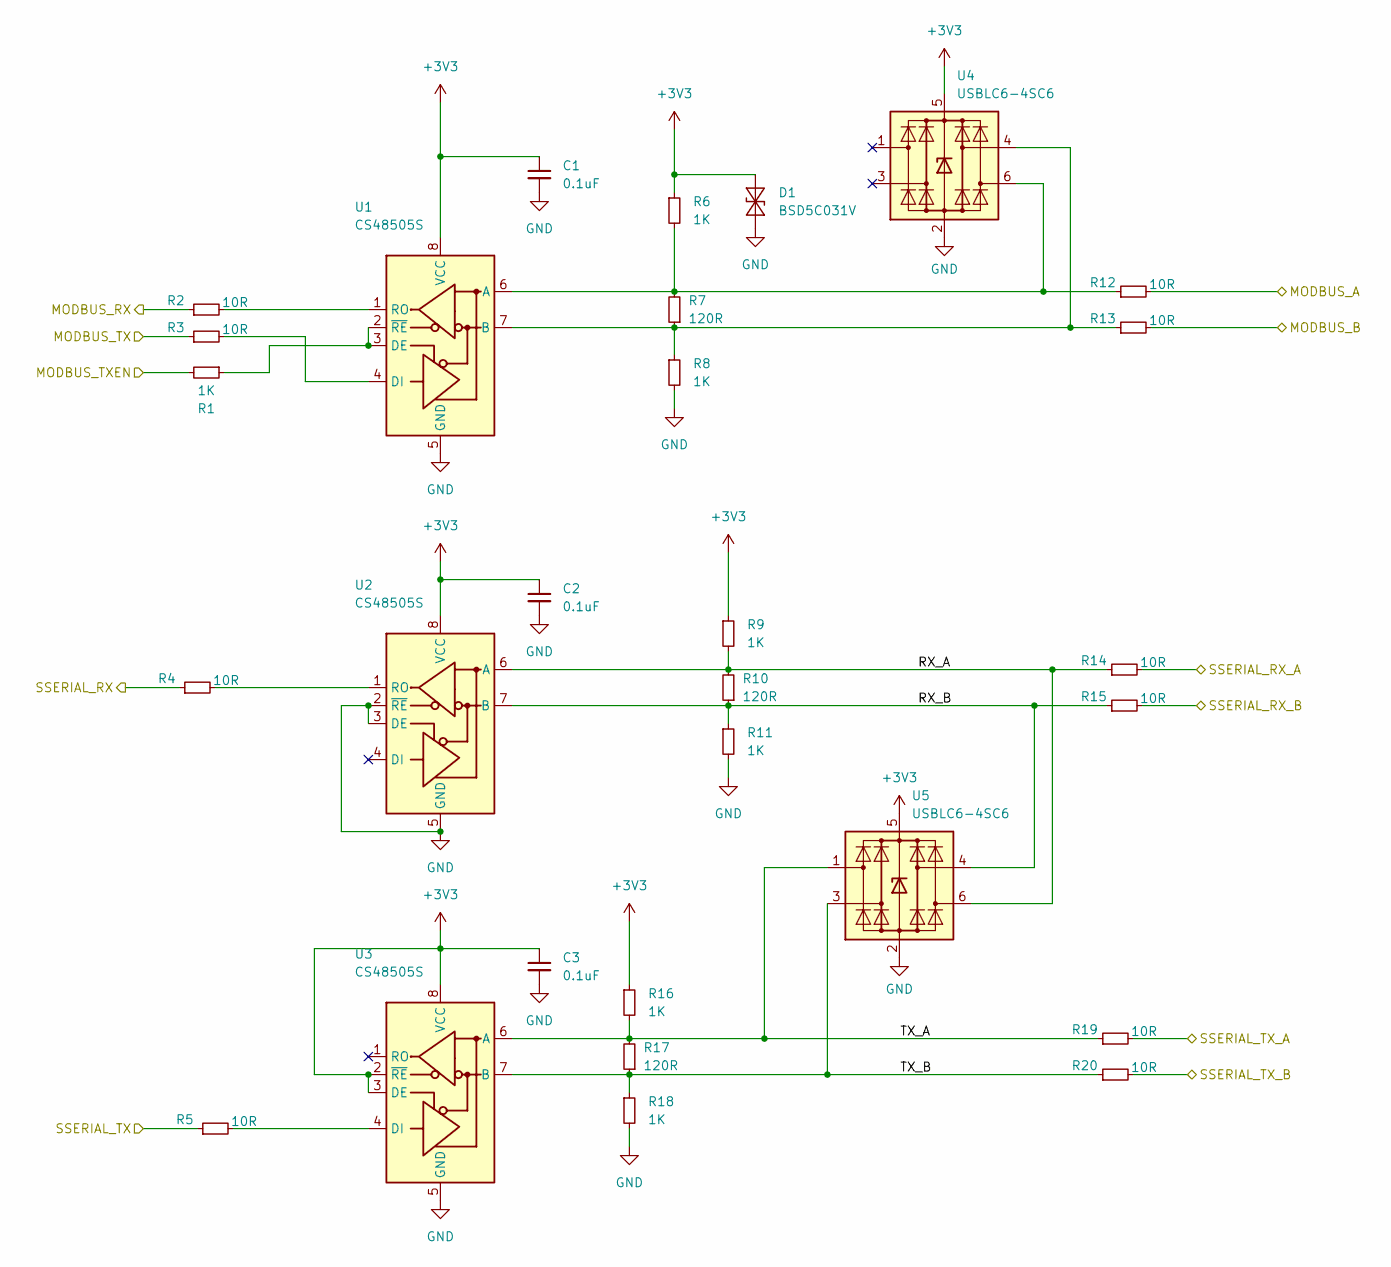
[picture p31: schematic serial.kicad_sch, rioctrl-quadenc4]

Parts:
C1, C2, C3: 0.1uF; C_0603_1608Metric; LCSC# C14663
D1: BSD5C031V; D_SOD-523; MPN BSD5C031V; LCSC# C151984
R1, R6, R8, R9, R11, R16, R18: 1K; R_0603_1608Metric; LCSC# C22548
R2, R3, R4, R5, R12, R13, R14, R15, R19, R20: 10R; R_0603_1608Metric; LCSC# C109318
R7, R10, R17: 120R; R_0603_1608Metric; LCSC# C114640
U1, U2, U3: CS48505S; SOIC-8_3.9x4.9mm_P1.27mm; MPN CS48505S; LCSC# C3202824
U4, U5: USBLC6-4SC6; SOT-23-6; MPN USBLC6-4SC6; LCSC# C5197386

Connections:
+3V3: C1.1, C2.1, C3.1, D1.1 (A1), R6.1, R9.1, R16.1, U1.8 (VCC), U2.8 (VCC), U3.2 (~RE), U3.3 (DE), U3.8 (VCC), U4.5 (VBUS), U5.5 (VBUS); also elsewhere on the board
/Serial/MODBUS_A: R12.2; also elsewhere on the board
/Serial/MODBUS_B: R13.2; also elsewhere on the board
/Serial/MODBUS_RX: R2.1; also elsewhere on the board
/Serial/MODBUS_TX: R3.1; also elsewhere on the board
/Serial/MODBUS_TXEN: R1.2; also elsewhere on the board
/Serial/RX_A: R9.2, R10.2, R14.1, U2.6 (A), U5.6 (I/O4)
/Serial/RX_B: R10.1, R11.1, R15.1, U2.7 (B), U5.4 (I/O3)
/Serial/SSERIAL_RX: R4.1; also elsewhere on the board
/Serial/SSERIAL_RX_A: R14.2; also elsewhere on the board
/Serial/SSERIAL_RX_B: R15.2; also elsewhere on the board
/Serial/SSERIAL_TX: R5.1; also elsewhere on the board
/Serial/SSERIAL_TX_A: R19.2; also elsewhere on the board
/Serial/SSERIAL_TX_B: R20.2; also elsewhere on the board
/Serial/TX_A: R16.2, R17.2, R19.1, U3.6 (A), U5.1 (I/O1)
/Serial/TX_B: R17.1, R18.1, R20.1, U3.7 (B), U5.3 (I/O2)
GND: C1.2, C2.2, C3.2, D1.2 (A2), R8.2, R11.2, R18.2, U1.5 (GND), U2.2 (~RE), U2.3 (DE), U2.5 (GND), U3.5 (GND), U4.2 (GND), U5.2 (GND); also elsewhere on the board
unnamed: R6.2, R7.2, R12.1, U1.6 (A), U4.6 (I/O4)
unnamed: R7.1, R8.1, R13.1, U1.7 (B), U4.4 (I/O3)
unnamed: R1.1, U1.2 (~RE), U1.3 (DE)
unnamed: R3.2, U1.4 (DI)
unnamed: R2.2, U1.1 (RO)
unnamed: R4.2, U2.1 (RO)
unnamed: R5.2, U3.4 (DI)

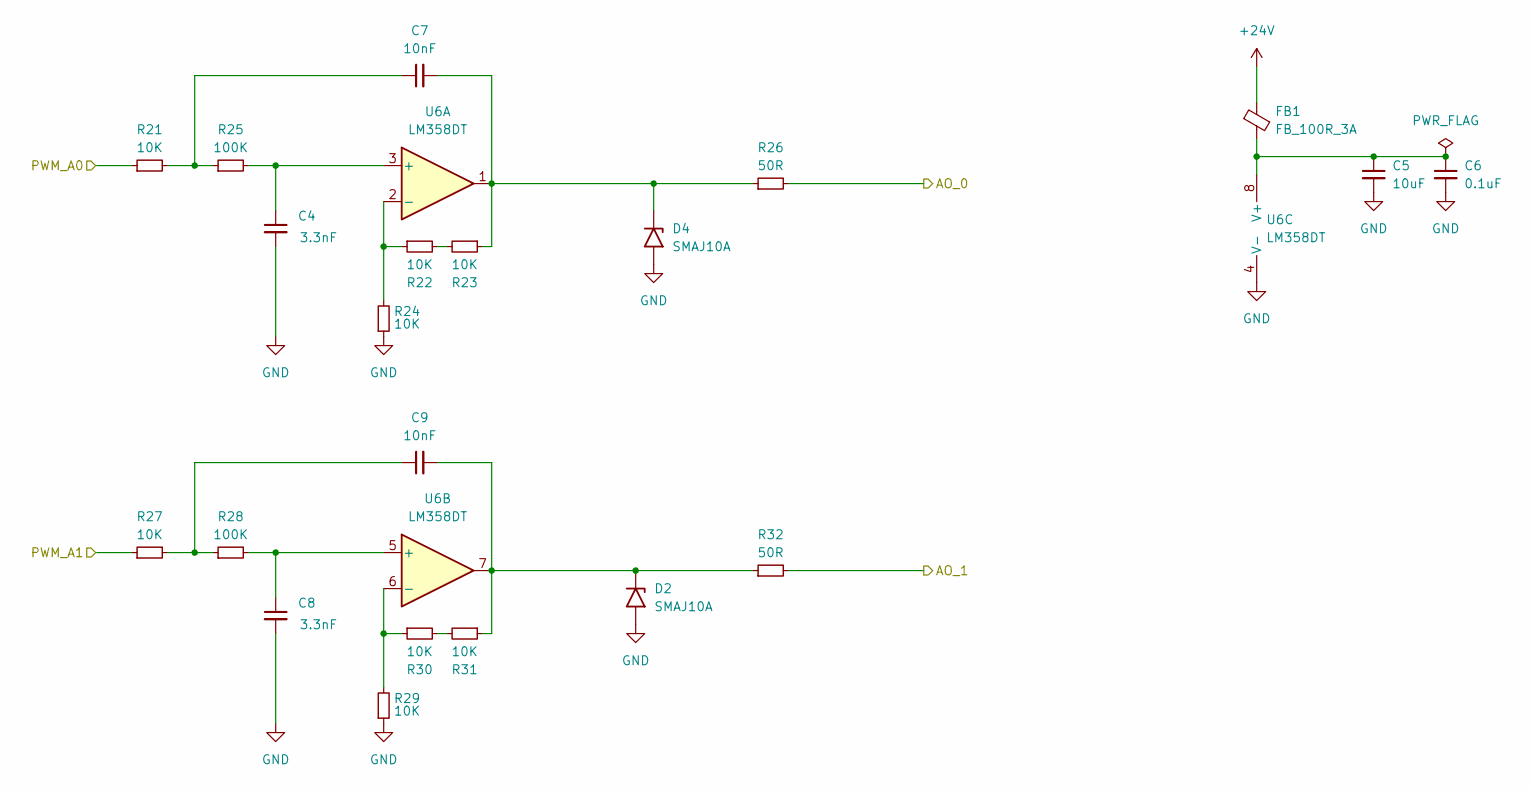
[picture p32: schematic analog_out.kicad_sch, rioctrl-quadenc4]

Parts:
C4, C8: 3.3nF; C_0603_1608Metric
C5: 10uF; C_0603_1608Metric
C6: 0.1uF; C_0603_1608Metric
C7, C9: 10nF; C_0603_1608Metric
D2, D4: SMAJ10A; D_SMA
FB1: FB_100R_3A; L_0603_1608Metric; MPN UPZ1608E101-3R0TF; LCSC# C96995
R21, R22, R23, R24, R27, R29, R30, R31: 10K; R_0603_1608Metric
R25, R28: 100K; R_0603_1608Metric
R26, R32: 50R; R_0603_1608Metric
U6: LM358DT; SO-8_3.9x4.9mm_P1.27mm; MPN LM358DT; LCSC# C9418

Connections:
+24V: FB1.1; also elsewhere on the board
/Analog outputs/AO_0: R26.2; also elsewhere on the board
/Analog outputs/AO_1: R32.2; also elsewhere on the board
/Analog outputs/PWM_A0: R21.1; also elsewhere on the board
/Analog outputs/PWM_A1: R27.1; also elsewhere on the board
GND: C4.2, C5.2, C6.2, C8.2, D2.2 (A2), D4.2 (A2), R24.1, R29.1, U6.4 (V-); also elsewhere on the board
unnamed: C7.1, R21.2, R25.1
unnamed: C9.1, R27.2, R28.1
unnamed: C9.2, D2.1 (A1), R31.1, R32.1, U6.7
unnamed: C7.2, D4.1 (A1), R23.1, R26.1, U6.1
unnamed: R22.2, R23.2
unnamed: R30.2, R31.2
unnamed: C4.1, R25.2, U6.3 (+)
unnamed: R22.1, R24.2, U6.2 (-)
unnamed: C8.1, R28.2, U6.5 (+)
unnamed: R29.2, R30.1, U6.6 (-)
unnamed: C5.1, C6.1, FB1.2, U6.8 (V+)

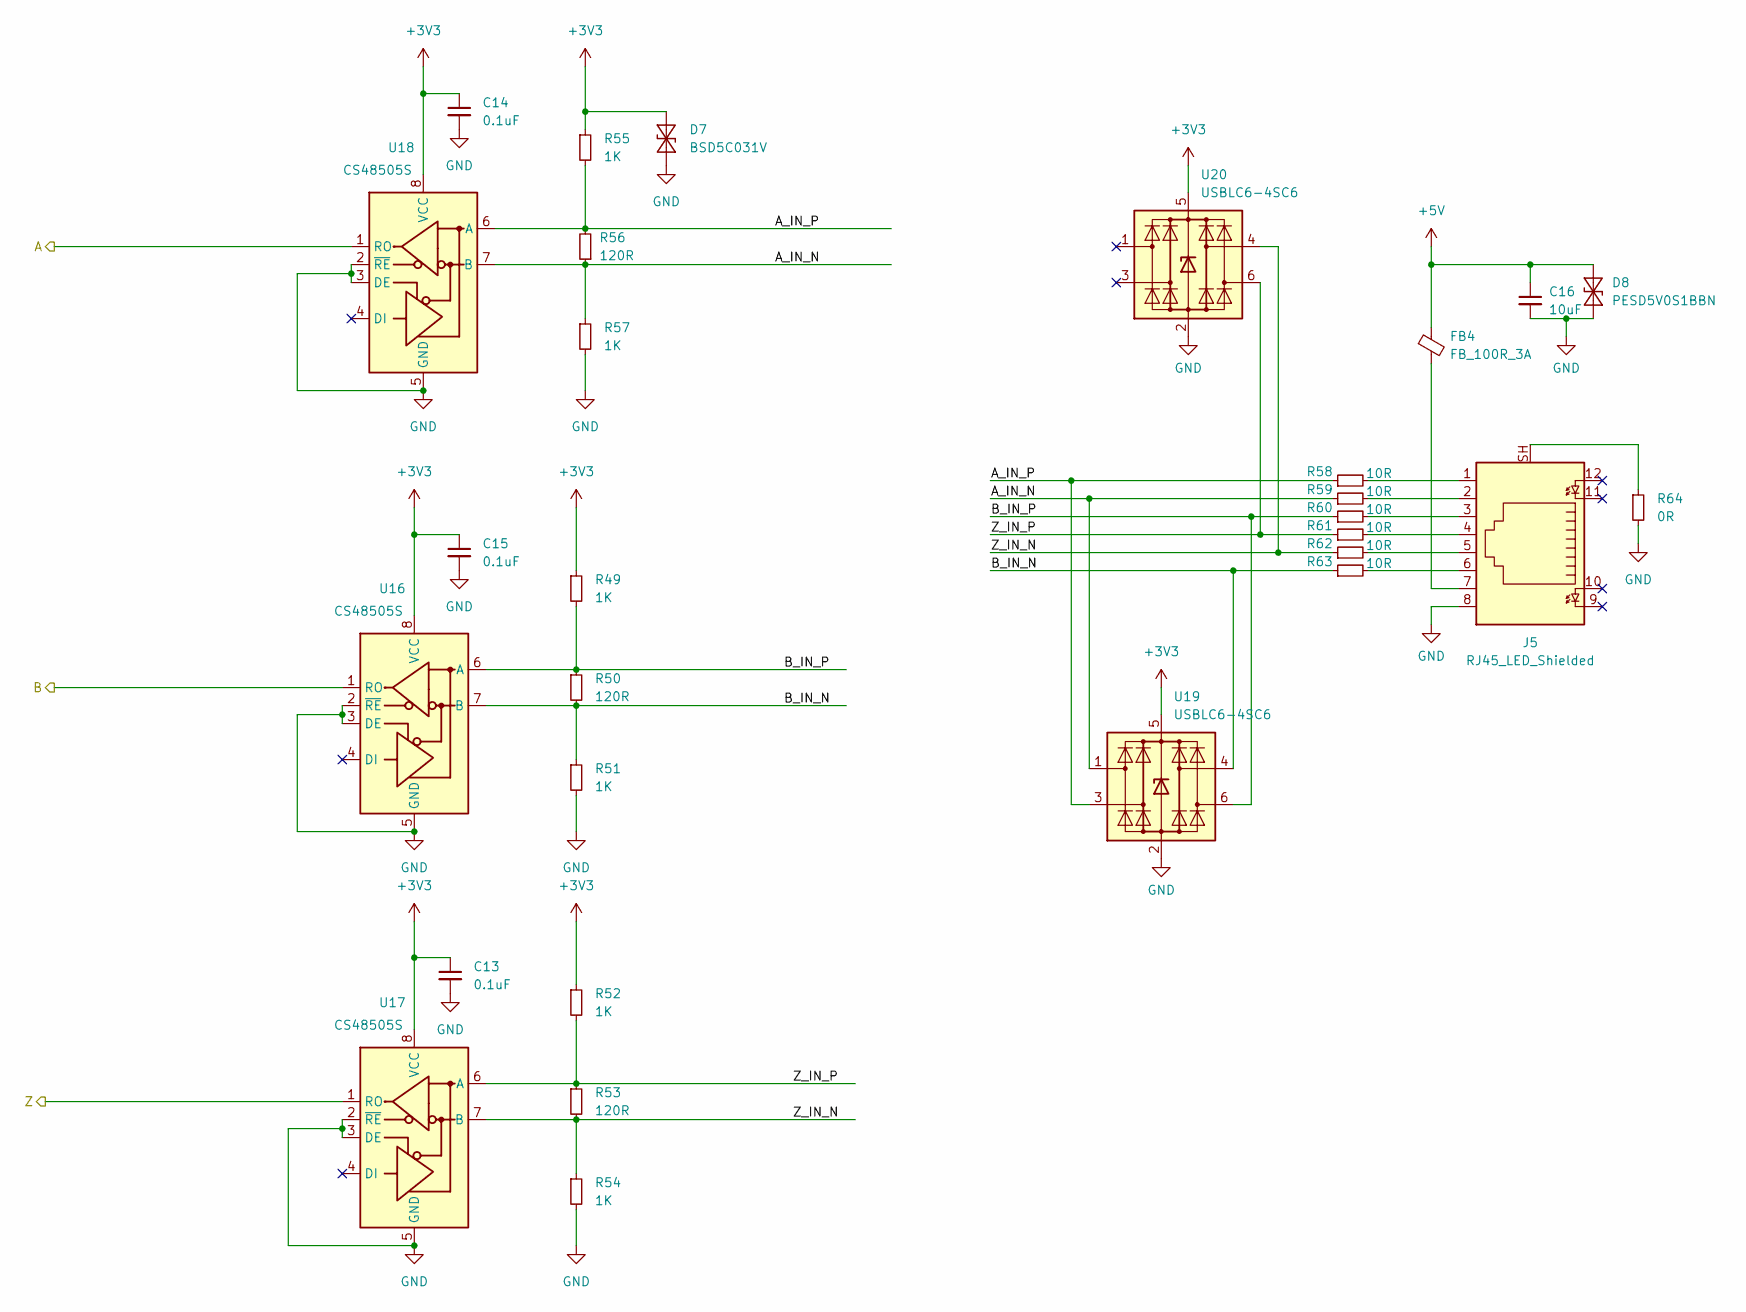
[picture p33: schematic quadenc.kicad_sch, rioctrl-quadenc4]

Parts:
C13, C14, C15: 0.1uF; C_0603_1608Metric; LCSC# C14663
C16: 10uF; C_0805_2012Metric; MPN GRM21BR61H106KE43L; LCSC# C440198
D7: BSD5C031V; D_SOD-523; MPN BSD5C031V; LCSC# C151984
D8: PESD5V0S1BBN; D_SOD-523; MPN PESD5V0S1BBN; LCSC# C314264
FB4: FB_100R_3A; L_0603_1608Metric; MPN UPZ1608E101-3R0TF; LCSC# C96995
J5: RJ45_LED_Shielded; R-RJ45R08P-C000; MPN R-RJ45R08P-C000; LCSC# C386757
R49, R51, R52, R54, R55, R57: 1K; R_0603_1608Metric; LCSC# C22548
R50, R53, R56: 120R; R_0603_1608Metric; LCSC# C114640
R58, R59, R60, R61, R62, R63: 10R; R_0603_1608Metric; LCSC# C109318
R64: 0R; R_0603_1608Metric; LCSC# C95177
U16, U17, U18: CS48505S; SOIC-8_3.9x4.9mm_P1.27mm; MPN CS48505S; LCSC# C3202824
U19, U20: USBLC6-4SC6; SOT-23-6; MPN USBLC6-4SC6; LCSC# C5197386

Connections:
+3V3: C13.1, C14.1, C15.1, D7.1 (A1), R49.1, R52.1, R55.1, U16.8 (VCC), U17.8 (VCC), U18.8 (VCC), U19.5 (VBUS), U20.5 (VBUS); also elsewhere on the board
+5V: C16.1, D8.2 (A2), FB4.1; also elsewhere on the board
/Quadenc/A: U18.1 (RO); also elsewhere on the board
/Quadenc/A_IN_N: R56.1, R57.1, R59.1, U18.7 (B), U19.1 (I/O1)
/Quadenc/A_IN_P: R55.2, R56.2, R58.1, U18.6 (A), U19.3 (I/O2)
/Quadenc/B: U16.1 (RO); also elsewhere on the board
/Quadenc/B_IN_N: R50.2, R51.1, R63.1, U16.7 (B), U19.4 (I/O3)
/Quadenc/B_IN_P: R49.2, R50.1, R60.1, U16.6 (A), U19.6 (I/O4)
/Quadenc/Z: U17.1 (RO); also elsewhere on the board
/Quadenc/Z_IN_N: R53.2, R54.1, R62.1, U17.7 (B), U20.4 (I/O3)
/Quadenc/Z_IN_P: R52.2, R53.1, R61.1, U17.6 (A), U20.6 (I/O4)
GND: C13.2, C14.2, C15.2, C16.2, D7.2 (A2), D8.1 (A1), J5.8, R51.2, R54.2, R57.2, R64.2, U16.2 (~RE), U16.3 (DE), U16.5 (GND), U17.2 (~RE), U17.3 (DE), U17.5 (GND), U18.2 (~RE), U18.3 (DE), U18.5 (GND), U19.2 (GND), U20.2 (GND); also elsewhere on the board
unnamed: FB4.2, J5.7
unnamed: J5.1, R58.2
unnamed: J5.2, R59.2
unnamed: J5.3, R60.2
unnamed: J5.4, R61.2
unnamed: J5.5, R62.2
unnamed: J5.6, R63.2
unnamed: J5.SH, R64.1

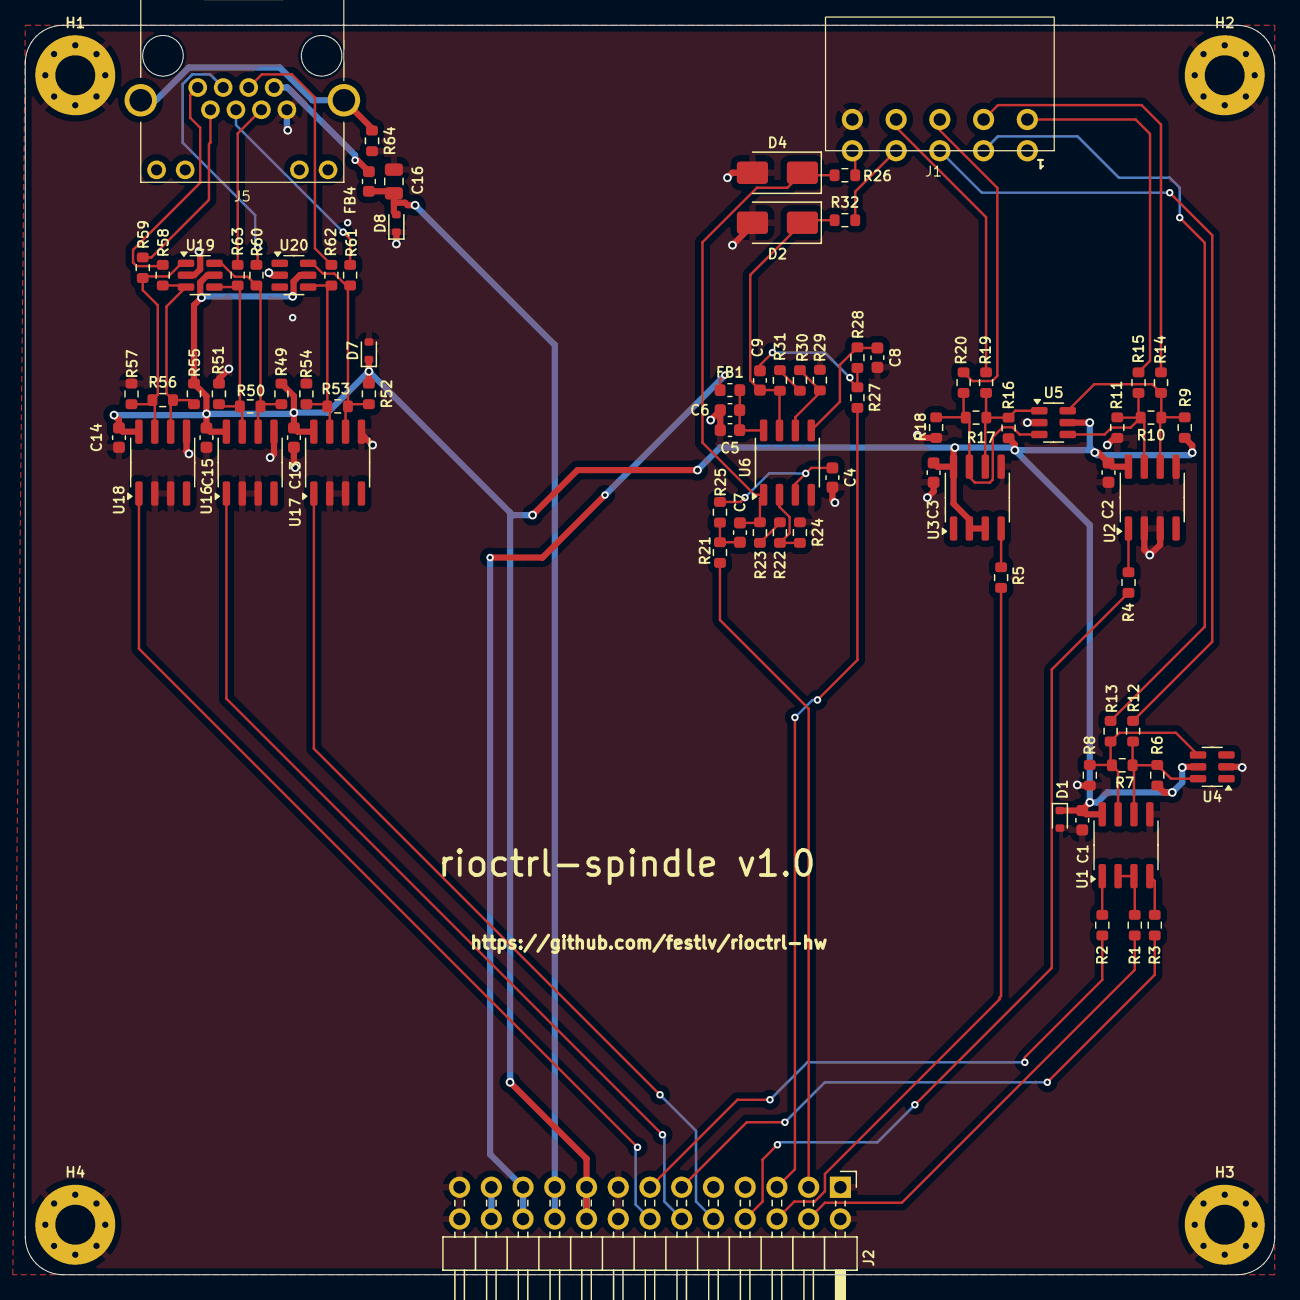
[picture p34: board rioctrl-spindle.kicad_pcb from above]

Board: 2 copper layers, 100.0 x 100.0 mm, 86 parts (0 on the bottom side), 59 nets.

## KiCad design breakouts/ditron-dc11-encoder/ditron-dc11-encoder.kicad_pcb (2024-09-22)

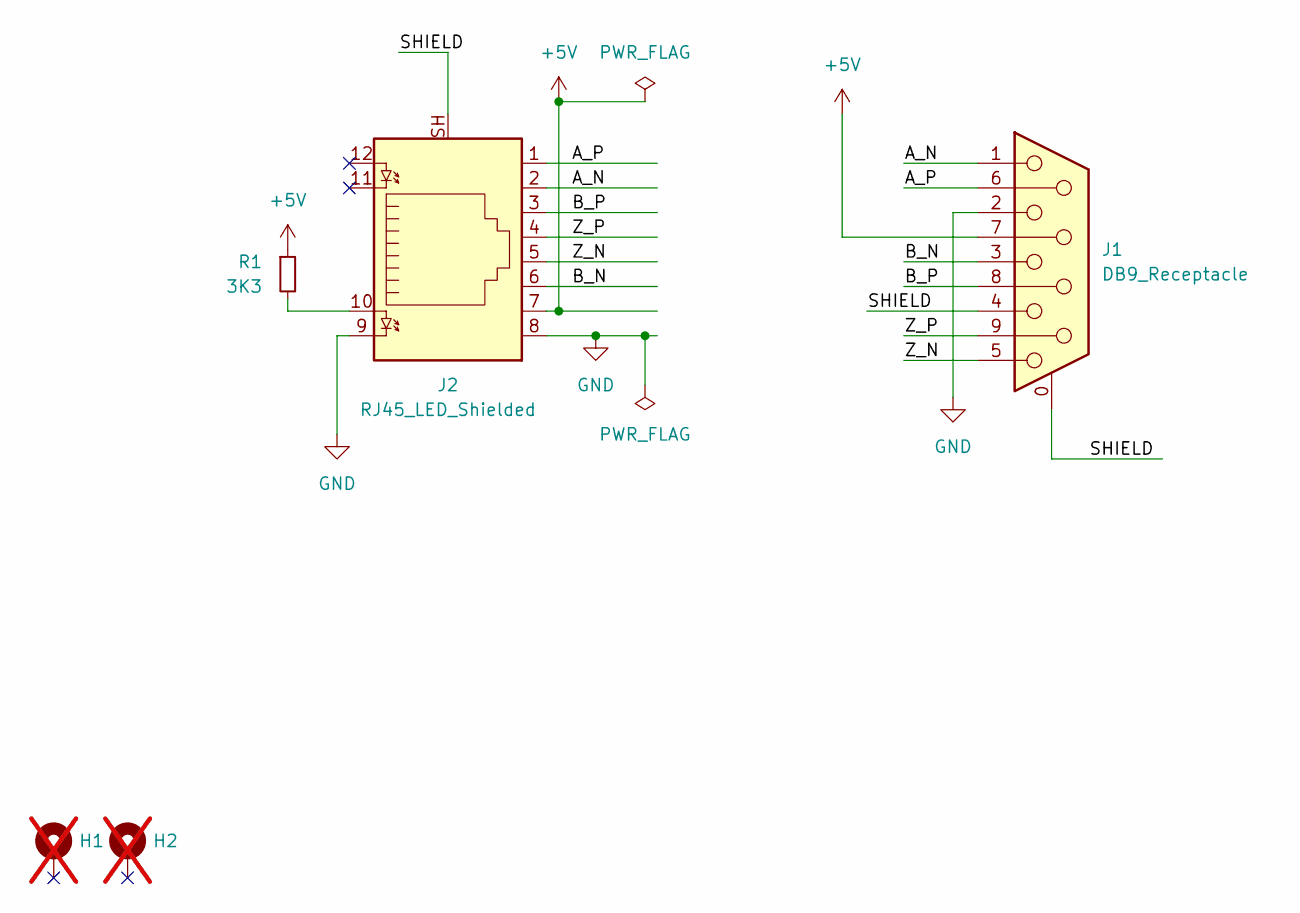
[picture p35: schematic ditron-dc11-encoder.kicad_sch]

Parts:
H1, H2: MH_3.2mm; MountingHole_3.2mm_M3_Pad_Via; not fitted
J1: DB9_Receptacle; DSUB-9_Female_Horizontal_P2.77x2.84mm_EdgePinOffset7.70mm_H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; MPN D-DMR009PF-D002; LCSC# C141882
J2: RJ45_LED_Shielded; R-RJ45R08P-C000; MPN R-RJ45R08P-C000; LCSC# C386757
R1: 3K3; R_0603_1608Metric; LCSC# C108078

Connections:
+5V: J1.7, J2.7, R1.1
/A_N: J1.1, J2.2
/A_P: J1.6, J2.1
/B_N: J1.3, J2.6
/B_P: J1.8, J2.3
/SHIELD: J1.0 (PAD), J1.4, J2.SH
/Z_N: J1.5, J2.5
/Z_P: J1.9, J2.4
GND: J1.2, J2.8, J2.9
unnamed: J2.10, R1.2

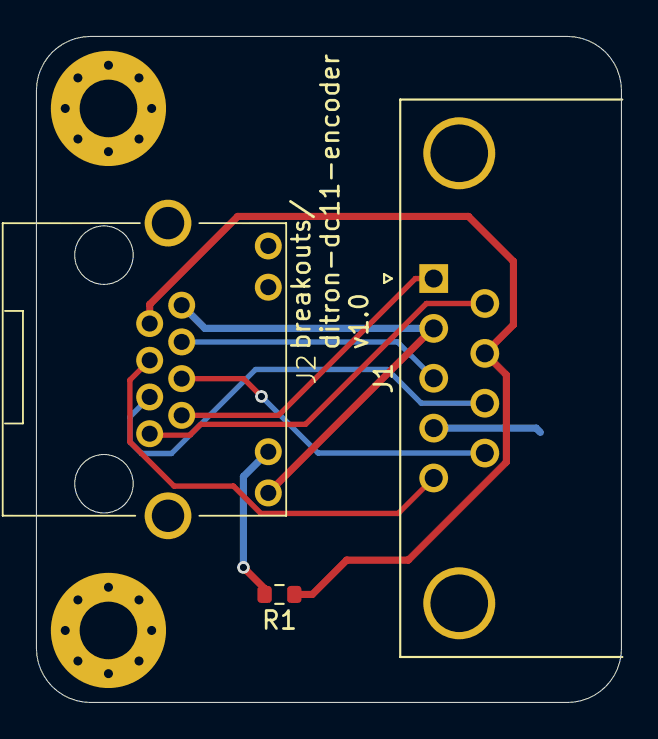
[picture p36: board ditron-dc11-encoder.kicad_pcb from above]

Board: 2 copper layers, 32.5 x 37.0 mm, 5 parts (0 on the bottom side), 10 nets.

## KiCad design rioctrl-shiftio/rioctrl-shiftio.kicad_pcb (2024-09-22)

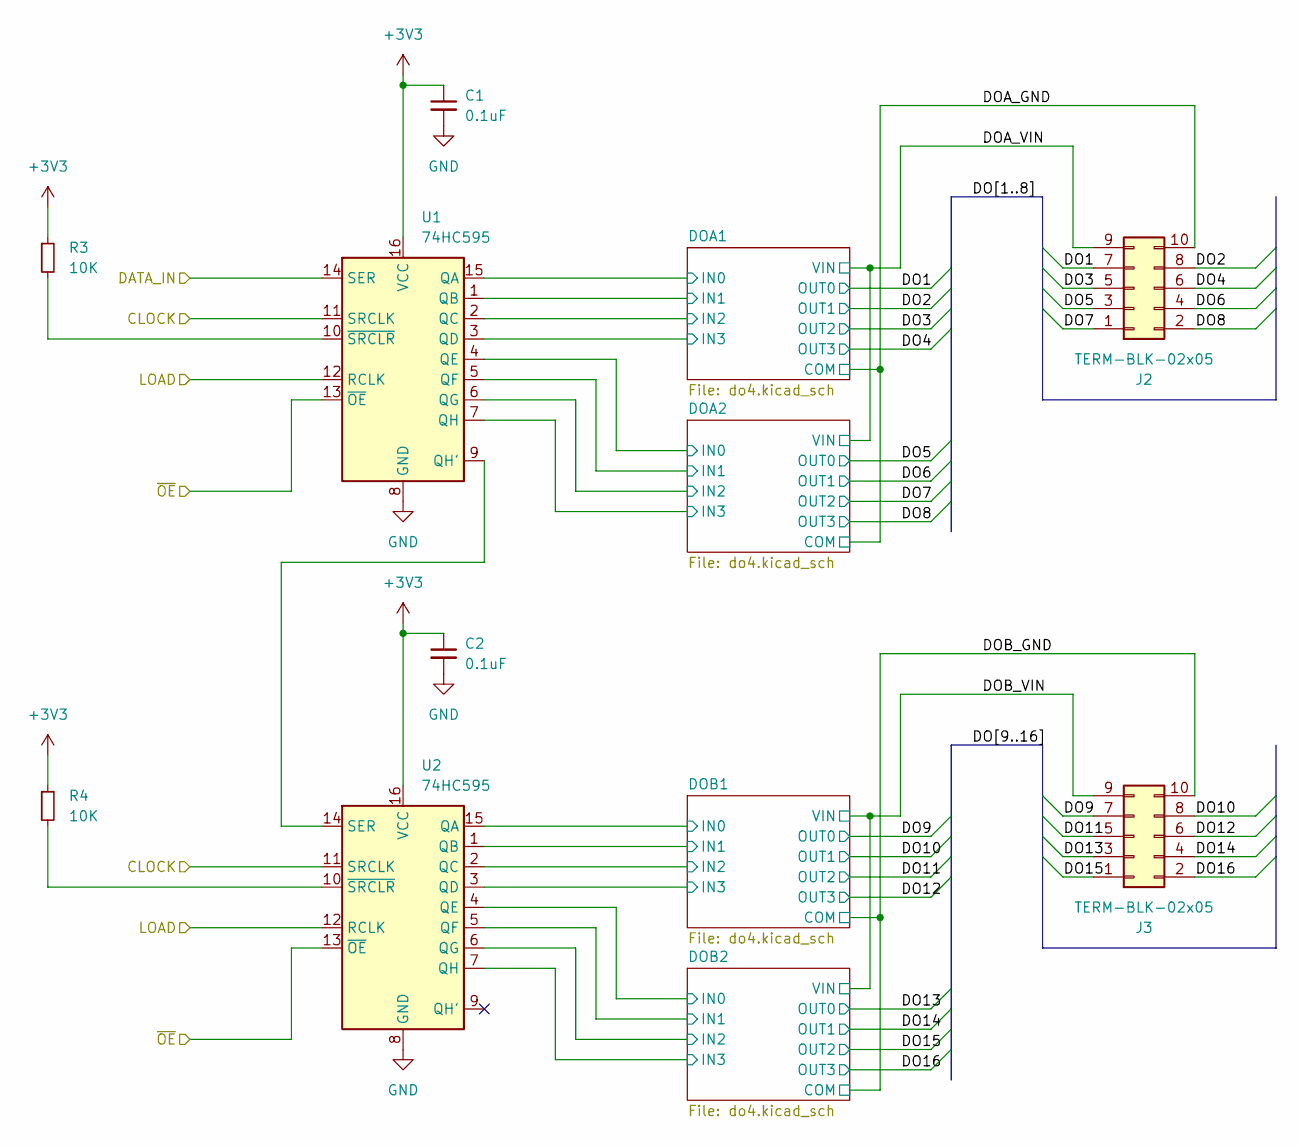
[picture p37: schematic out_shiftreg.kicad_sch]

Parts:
C1, C2: 0.1uF; C_0603_1608Metric; LCSC# C14663
J2, J3: TERM-BLK-02x05; JL15EDGRHC-35005B02; MPN JL15EDGRHC-35005B02; LCSC# C2908411
R3, R4: 10K; R_0603_1608Metric; LCSC# C98220
U1, U2: 74HC595; SO-16_3.9x9.9mm_P1.27mm; MPN 74HC595D,118; LCSC# C5947

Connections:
+3V3: C1.1, C2.1, R3.1, R4.1, U1.16 (VCC), U2.16 (VCC); also elsewhere on the board
/Output shiftreg/CLOCK: U1.11 (SRCLK), U2.11 (SRCLK); also elsewhere on the board
/Output shiftreg/DATA_IN: U1.14 (SER); also elsewhere on the board
/Output shiftreg/DO1: J2.7; also elsewhere on the board
/Output shiftreg/DO2: J2.8; also elsewhere on the board
/Output shiftreg/DO3: J2.5; also elsewhere on the board
/Output shiftreg/DO4: J2.6; also elsewhere on the board
/Output shiftreg/DO5: J2.3; also elsewhere on the board
/Output shiftreg/DO6: J2.4; also elsewhere on the board
/Output shiftreg/DO7: J2.1; also elsewhere on the board
/Output shiftreg/DO8: J2.2; also elsewhere on the board
/Output shiftreg/DO9: J3.7; also elsewhere on the board
/Output shiftreg/DO10: J3.8; also elsewhere on the board
/Output shiftreg/DO11: J3.5; also elsewhere on the board
/Output shiftreg/DO12: J3.6; also elsewhere on the board
/Output shiftreg/DO13: J3.3; also elsewhere on the board
/Output shiftreg/DO14: J3.4; also elsewhere on the board
/Output shiftreg/DO15: J3.1; also elsewhere on the board
/Output shiftreg/DO16: J3.2; also elsewhere on the board
/Output shiftreg/DOA1/IN0: U1.15 (QA); also elsewhere on the board
/Output shiftreg/DOA1/IN1: U1.1 (QB); also elsewhere on the board
/Output shiftreg/DOA1/IN2: U1.2 (QC); also elsewhere on the board
/Output shiftreg/DOA1/IN3: U1.3 (QD); also elsewhere on the board
/Output shiftreg/DOA2/IN0: U1.4 (QE); also elsewhere on the board
/Output shiftreg/DOA2/IN1: U1.5 (QF); also elsewhere on the board
/Output shiftreg/DOA2/IN2: U1.6 (QG); also elsewhere on the board
/Output shiftreg/DOA2/IN3: U1.7 (QH); also elsewhere on the board
/Output shiftreg/DOA_GND: J2.10; also elsewhere on the board
/Output shiftreg/DOA_VIN: J2.9; also elsewhere on the board
/Output shiftreg/DOB1/IN0: U2.15 (QA); also elsewhere on the board
/Output shiftreg/DOB1/IN1: U2.1 (QB); also elsewhere on the board
/Output shiftreg/DOB1/IN2: U2.2 (QC); also elsewhere on the board
/Output shiftreg/DOB1/IN3: U2.3 (QD); also elsewhere on the board
/Output shiftreg/DOB2/IN0: U2.4 (QE); also elsewhere on the board
/Output shiftreg/DOB2/IN1: U2.5 (QF); also elsewhere on the board
/Output shiftreg/DOB2/IN2: U2.6 (QG); also elsewhere on the board
/Output shiftreg/DOB2/IN3: U2.7 (QH); also elsewhere on the board
/Output shiftreg/DOB_GND: J3.10; also elsewhere on the board
/Output shiftreg/DOB_VIN: J3.9; also elsewhere on the board
/Output shiftreg/LOAD: U1.12 (RCLK), U2.12 (RCLK); also elsewhere on the board
/Output shiftreg/~OE: U1.13 (~OE), U2.13 (~OE); also elsewhere on the board
GND: C1.2, C2.2, U1.8 (GND), U2.8 (GND); also elsewhere on the board
unnamed: U1.9 (QH'), U2.14 (SER)
unnamed: R3.2, U1.10 (~SRCLR)
unnamed: R4.2, U2.10 (~SRCLR)

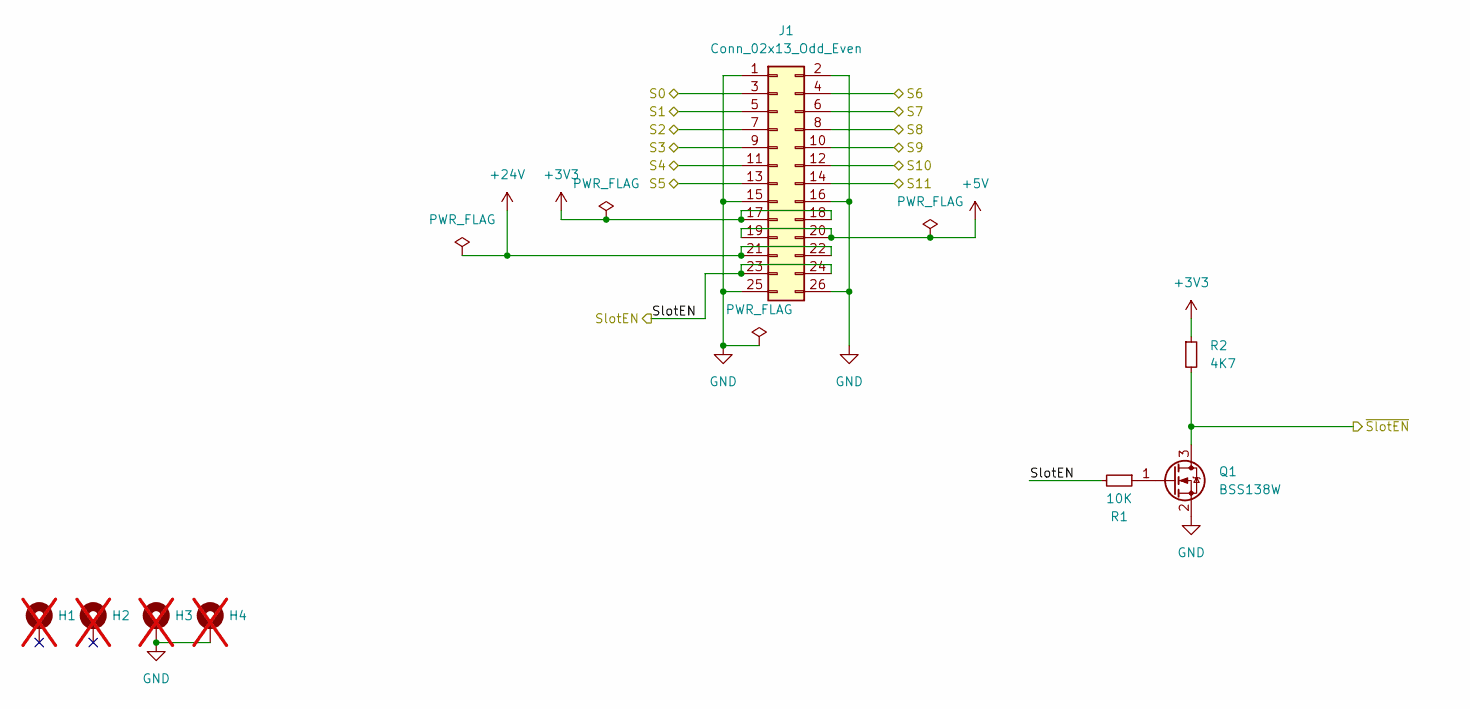
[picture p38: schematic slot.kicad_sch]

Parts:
H1, H2, H3, H4: MH_3.2mm; MountingHole_3.2mm_M3_Pad_Via; not fitted
J1: Conn_02x13_Odd_Even; PinHeader_2x13_P2.54mm_Horizontal; LCSC# C2894993
Q1: BSS138W; SOT-323_SC-70; MPN BSS138W; LCSC# C504052
R1: 10K; R_0603_1608Metric; LCSC# C98220
R2: 4K7; R_0603_1608Metric; LCSC# C99782

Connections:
+3V3: J1.17, J1.18, R2.1; also elsewhere on the board
+5V: J1.19, J1.20
+24V: J1.21, J1.22
/Input shiftreg/CLK: J1.11; also elsewhere on the board
/Input shiftreg/DATA_OUT: J1.9; also elsewhere on the board
/Input shiftreg/LOAD: J1.13; also elsewhere on the board
/Output shiftreg/CLOCK: J1.5; also elsewhere on the board
/Output shiftreg/DATA_IN: J1.3; also elsewhere on the board
/Output shiftreg/LOAD: J1.7; also elsewhere on the board
/Output shiftreg/~OE: Q1.3 (D), R2.2; also elsewhere on the board
/Slot/S6: J1.4
/Slot/S7: J1.6
/Slot/S8: J1.8
/Slot/S9: J1.10
/Slot/S10: J1.12
/Slot/S11: J1.14
/Slot/SlotEN: J1.23, J1.24, R1.2
GND: H3.1, H4.1, J1.1, J1.2, J1.15, J1.16, J1.25, J1.26, Q1.2 (S); also elsewhere on the board
unnamed: Q1.1 (G), R1.1

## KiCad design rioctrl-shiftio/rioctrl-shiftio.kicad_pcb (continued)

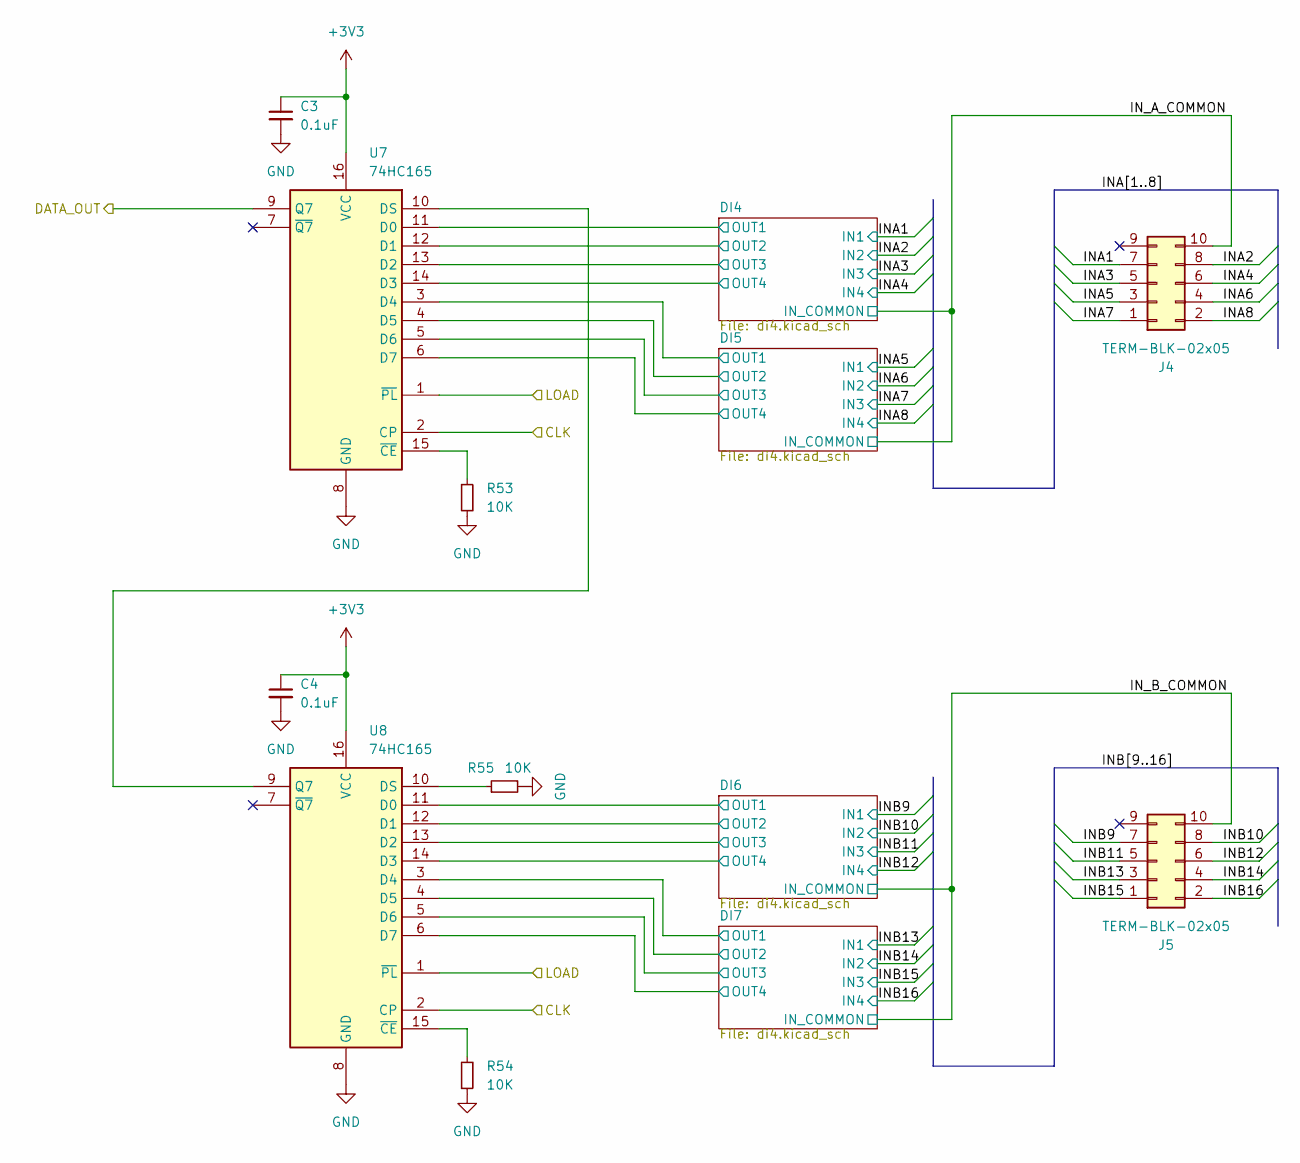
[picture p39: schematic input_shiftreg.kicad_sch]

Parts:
C3, C4: 0.1uF; C_0603_1608Metric; LCSC# C14663
J4, J5: TERM-BLK-02x05; JL15EDGRHC-35005B02; MPN JL15EDGRHC-35005B02; LCSC# C2908411
R53, R54, R55: 10K; R_0603_1608Metric; LCSC# C98220
U7, U8: 74HC165; SO-16_3.9x9.9mm_P1.27mm; MPN 74HC165D,653; LCSC# C5613

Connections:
+3V3: C3.1, C4.1, U7.16 (VCC), U8.16 (VCC); also elsewhere on the board
/Input shiftreg/CLK: U7.2 (CP), U8.2 (CP); also elsewhere on the board
/Input shiftreg/DATA_OUT: U7.9 (Q7); also elsewhere on the board
/Input shiftreg/DI4/OUT1: U7.11 (D0); also elsewhere on the board
/Input shiftreg/DI4/OUT2: U7.12 (D1); also elsewhere on the board
/Input shiftreg/DI4/OUT3: U7.13 (D2); also elsewhere on the board
/Input shiftreg/DI4/OUT4: U7.14 (D3); also elsewhere on the board
/Input shiftreg/DI5/OUT1: U7.3 (D4); also elsewhere on the board
/Input shiftreg/DI5/OUT2: U7.4 (D5); also elsewhere on the board
/Input shiftreg/DI5/OUT3: U7.5 (D6); also elsewhere on the board
/Input shiftreg/DI5/OUT4: U7.6 (D7); also elsewhere on the board
/Input shiftreg/DI6/OUT1: U8.11 (D0); also elsewhere on the board
/Input shiftreg/DI6/OUT2: U8.12 (D1); also elsewhere on the board
/Input shiftreg/DI6/OUT3: U8.13 (D2); also elsewhere on the board
/Input shiftreg/DI6/OUT4: U8.14 (D3); also elsewhere on the board
/Input shiftreg/DI7/OUT1: U8.3 (D4); also elsewhere on the board
/Input shiftreg/DI7/OUT2: U8.4 (D5); also elsewhere on the board
/Input shiftreg/DI7/OUT3: U8.5 (D6); also elsewhere on the board
/Input shiftreg/DI7/OUT4: U8.6 (D7); also elsewhere on the board
/Input shiftreg/INA1: J4.7; also elsewhere on the board
/Input shiftreg/INA2: J4.8; also elsewhere on the board
/Input shiftreg/INA3: J4.5; also elsewhere on the board
/Input shiftreg/INA4: J4.6; also elsewhere on the board
/Input shiftreg/INA5: J4.3; also elsewhere on the board
/Input shiftreg/INA6: J4.4; also elsewhere on the board
/Input shiftreg/INA7: J4.1; also elsewhere on the board
/Input shiftreg/INA8: J4.2; also elsewhere on the board
/Input shiftreg/INB9: J5.7; also elsewhere on the board
/Input shiftreg/INB10: J5.8; also elsewhere on the board
/Input shiftreg/INB11: J5.5; also elsewhere on the board
/Input shiftreg/INB12: J5.6; also elsewhere on the board
/Input shiftreg/INB13: J5.3; also elsewhere on the board
/Input shiftreg/INB14: J5.4; also elsewhere on the board
/Input shiftreg/INB15: J5.1; also elsewhere on the board
/Input shiftreg/INB16: J5.2; also elsewhere on the board
/Input shiftreg/IN_A_COMMON: J4.10; also elsewhere on the board
/Input shiftreg/IN_B_COMMON: J5.10; also elsewhere on the board
/Input shiftreg/LOAD: U7.1 (~PL), U8.1 (~PL); also elsewhere on the board
GND: C3.2, C4.2, R53.2, R54.2, R55.2, U7.8 (GND), U8.8 (GND); also elsewhere on the board
unnamed: U7.10 (DS), U8.9 (Q7)
unnamed: R53.1, U7.15 (~CE)
unnamed: R55.1, U8.10 (DS)
unnamed: R54.1, U8.15 (~CE)

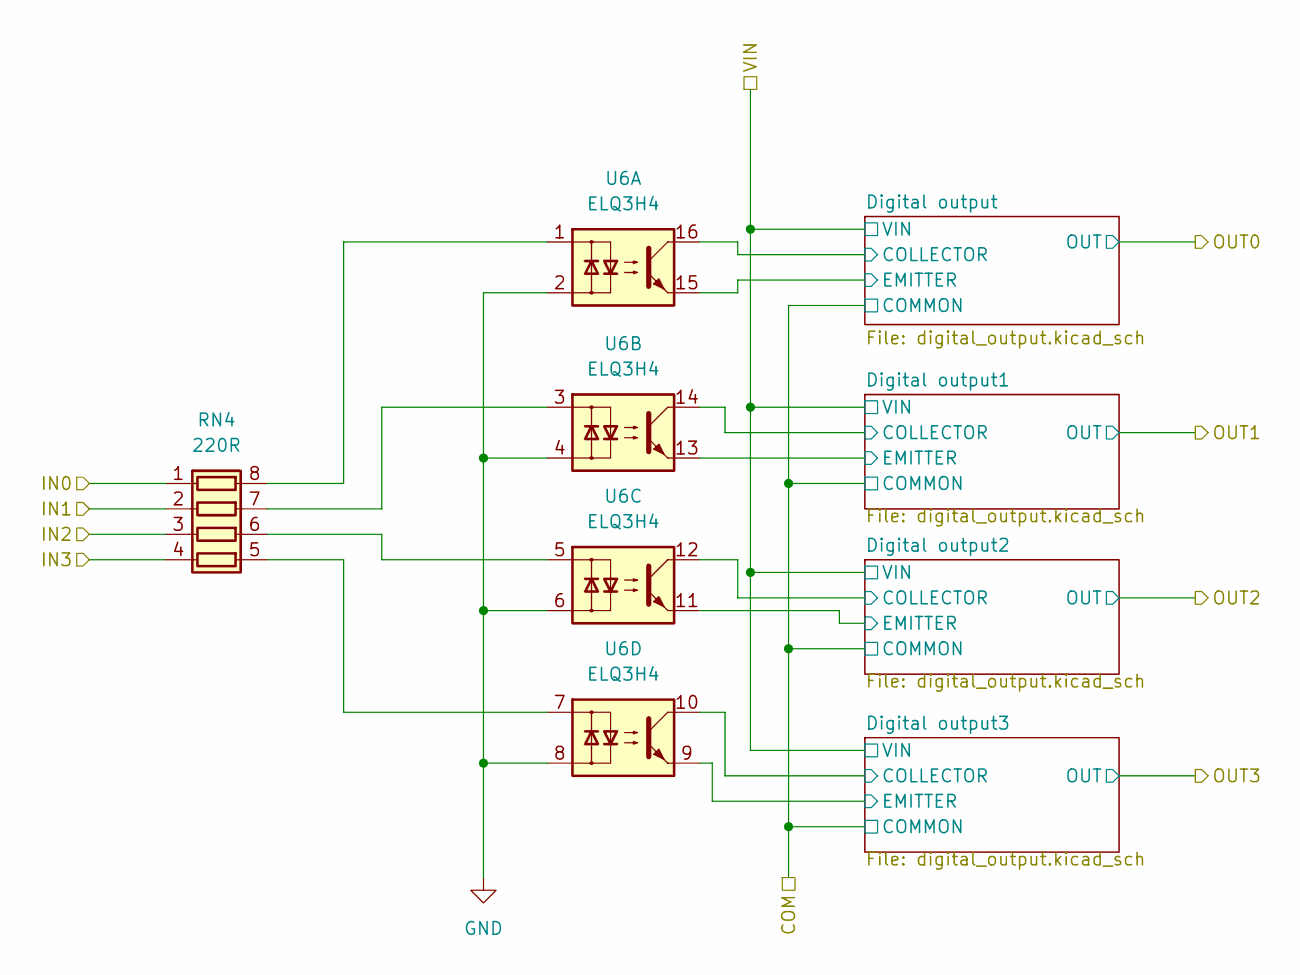
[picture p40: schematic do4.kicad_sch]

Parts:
RN4: 220R; R_Array_Convex_4x0603; LCSC# C706474
U6: ELQ3H4; SOIC-16W_5.3x10.2mm_P1.27mm; MPN ELQ3H4(TA)-G; LCSC# C150957

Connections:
/Output shiftreg/DOB2/Digital output1/COLLECTOR: U6.14; also elsewhere on the board
/Output shiftreg/DOB2/Digital output1/EMITTER: U6.13; also elsewhere on the board
/Output shiftreg/DOB2/Digital output2/COLLECTOR: U6.12; also elsewhere on the board
/Output shiftreg/DOB2/Digital output2/EMITTER: U6.11; also elsewhere on the board
/Output shiftreg/DOB2/Digital output3/COLLECTOR: U6.10; also elsewhere on the board
/Output shiftreg/DOB2/Digital output3/EMITTER: U6.9; also elsewhere on the board
/Output shiftreg/DOB2/Digital output/COLLECTOR: U6.16; also elsewhere on the board
/Output shiftreg/DOB2/Digital output/EMITTER: U6.15; also elsewhere on the board
/Output shiftreg/DOB2/IN0: RN4.1 (R1.1); also elsewhere on the board
/Output shiftreg/DOB2/IN1: RN4.2 (R2.1); also elsewhere on the board
/Output shiftreg/DOB2/IN2: RN4.3 (R3.1); also elsewhere on the board
/Output shiftreg/DOB2/IN3: RN4.4 (R4.1); also elsewhere on the board
GND: U6.2, U6.4, U6.6, U6.8; also elsewhere on the board
unnamed: RN4.8 (R1.2), U6.1
unnamed: RN4.7 (R2.2), U6.3
unnamed: RN4.6 (R3.2), U6.5
unnamed: RN4.5 (R4.2), U6.7

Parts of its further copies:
RN1, RN2, RN3: 220R; R_Array_Convex_4x0603; LCSC# C706474
U3, U4, U5: ELQ3H4; SOIC-16W_5.3x10.2mm_P1.27mm; MPN ELQ3H4(TA)-G; LCSC# C150957

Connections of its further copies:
/Output shiftreg/DOA1/Digital output1/COLLECTOR: U3.14; also elsewhere on the board
/Output shiftreg/DOA1/Digital output1/EMITTER: U3.13; also elsewhere on the board
/Output shiftreg/DOA1/Digital output2/COLLECTOR: U3.12; also elsewhere on the board
/Output shiftreg/DOA1/Digital output2/EMITTER: U3.11; also elsewhere on the board
/Output shiftreg/DOA1/Digital output3/COLLECTOR: U3.10; also elsewhere on the board
/Output shiftreg/DOA1/Digital output3/EMITTER: U3.9; also elsewhere on the board
/Output shiftreg/DOA1/Digital output/COLLECTOR: U3.16; also elsewhere on the board
/Output shiftreg/DOA1/Digital output/EMITTER: U3.15; also elsewhere on the board
/Output shiftreg/DOA1/IN0: RN1.1 (R1.1); also elsewhere on the board
/Output shiftreg/DOA1/IN1: RN1.2 (R2.1); also elsewhere on the board
/Output shiftreg/DOA1/IN2: RN1.3 (R3.1); also elsewhere on the board
/Output shiftreg/DOA1/IN3: RN1.4 (R4.1); also elsewhere on the board
/Output shiftreg/DOA2/Digital output1/COLLECTOR: U4.14; also elsewhere on the board
/Output shiftreg/DOA2/Digital output1/EMITTER: U4.13; also elsewhere on the board
/Output shiftreg/DOA2/Digital output2/COLLECTOR: U4.12; also elsewhere on the board
/Output shiftreg/DOA2/Digital output2/EMITTER: U4.11; also elsewhere on the board
/Output shiftreg/DOA2/Digital output3/COLLECTOR: U4.10; also elsewhere on the board
/Output shiftreg/DOA2/Digital output3/EMITTER: U4.9; also elsewhere on the board
/Output shiftreg/DOA2/Digital output/COLLECTOR: U4.16; also elsewhere on the board
/Output shiftreg/DOA2/Digital output/EMITTER: U4.15; also elsewhere on the board
/Output shiftreg/DOA2/IN0: RN2.1 (R1.1); also elsewhere on the board
/Output shiftreg/DOA2/IN1: RN2.2 (R2.1); also elsewhere on the board
/Output shiftreg/DOA2/IN2: RN2.3 (R3.1); also elsewhere on the board
/Output shiftreg/DOA2/IN3: RN2.4 (R4.1); also elsewhere on the board
/Output shiftreg/DOB1/Digital output1/COLLECTOR: U5.14; also elsewhere on the board
/Output shiftreg/DOB1/Digital output1/EMITTER: U5.13; also elsewhere on the board
/Output shiftreg/DOB1/Digital output2/COLLECTOR: U5.12; also elsewhere on the board
/Output shiftreg/DOB1/Digital output2/EMITTER: U5.11; also elsewhere on the board
/Output shiftreg/DOB1/Digital output3/COLLECTOR: U5.10; also elsewhere on the board
/Output shiftreg/DOB1/Digital output3/EMITTER: U5.9; also elsewhere on the board
/Output shiftreg/DOB1/Digital output/COLLECTOR: U5.16; also elsewhere on the board
/Output shiftreg/DOB1/Digital output/EMITTER: U5.15; also elsewhere on the board
/Output shiftreg/DOB1/IN0: RN3.1 (R1.1); also elsewhere on the board
/Output shiftreg/DOB1/IN1: RN3.2 (R2.1); also elsewhere on the board
/Output shiftreg/DOB1/IN2: RN3.3 (R3.1); also elsewhere on the board
/Output shiftreg/DOB1/IN3: RN3.4 (R4.1); also elsewhere on the board
GND: U3.2, U3.4, U3.6, U3.8, U4.2, U4.4, U4.6, U4.8, U5.2, U5.4, U5.6, U5.8; also elsewhere on the board
unnamed: RN1.8 (R1.2), U3.1
unnamed: RN1.7 (R2.2), U3.3
unnamed: RN1.6 (R3.2), U3.5
unnamed: RN1.5 (R4.2), U3.7
unnamed: RN2.8 (R1.2), U4.1
unnamed: RN2.7 (R2.2), U4.3
unnamed: RN2.6 (R3.2), U4.5
unnamed: RN2.5 (R4.2), U4.7
unnamed: RN3.8 (R1.2), U5.1
unnamed: RN3.7 (R2.2), U5.3
unnamed: RN3.6 (R3.2), U5.5
unnamed: RN3.5 (R4.2), U5.7


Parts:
RN11, RN12: 4.12K; R_Array_Convex_4x0603; LCSC# C728970
U12: ELQ3H4; SOIC-16W_5.3x10.2mm_P1.27mm; MPN ELQ3H4(TA)-G; LCSC# C150957

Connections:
+3V3: RN11.1 (R1.1), RN11.2 (R2.1), RN11.3 (R3.1), RN11.4 (R4.1); also elsewhere on the board
/Input shiftreg/DI7/OUT1: RN11.8 (R1.2), U12.10; also elsewhere on the board
/Input shiftreg/DI7/OUT2: RN11.7 (R2.2), U12.12; also elsewhere on the board
/Input shiftreg/DI7/OUT3: RN11.6 (R3.2), U12.14; also elsewhere on the board
/Input shiftreg/DI7/OUT4: RN11.5 (R4.2), U12.16; also elsewhere on the board
/Input shiftreg/INB13: RN12.8 (R1.2); also elsewhere on the board
/Input shiftreg/INB14: RN12.7 (R2.2); also elsewhere on the board
/Input shiftreg/INB15: RN12.6 (R3.2); also elsewhere on the board
/Input shiftreg/INB16: RN12.5 (R4.2); also elsewhere on the board
/Input shiftreg/IN_B_COMMON: U12.2, U12.4, U12.6, U12.8; also elsewhere on the board
GND: U12.9, U12.11, U12.13, U12.15; also elsewhere on the board
unnamed: RN12.1 (R1.1), U12.7
unnamed: RN12.2 (R2.1), U12.5
unnamed: RN12.3 (R3.1), U12.3
unnamed: RN12.4 (R4.1), U12.1

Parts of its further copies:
RN5, RN6, RN7, RN8, RN9, RN10: 4.12K; R_Array_Convex_4x0603; LCSC# C728970
U9, U10, U11: ELQ3H4; SOIC-16W_5.3x10.2mm_P1.27mm; MPN ELQ3H4(TA)-G; LCSC# C150957

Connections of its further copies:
+3V3: RN5.1 (R1.1), RN5.2 (R2.1), RN5.3 (R3.1), RN5.4 (R4.1), RN7.1 (R1.1), RN7.2 (R2.1), RN7.3 (R3.1), RN7.4 (R4.1), RN9.1 (R1.1), RN9.2 (R2.1), RN9.3 (R3.1), RN9.4 (R4.1); also elsewhere on the board
/Input shiftreg/DI4/OUT1: RN5.8 (R1.2), U9.10; also elsewhere on the board
/Input shiftreg/DI4/OUT2: RN5.7 (R2.2), U9.12; also elsewhere on the board
/Input shiftreg/DI4/OUT3: RN5.6 (R3.2), U9.14; also elsewhere on the board
/Input shiftreg/DI4/OUT4: RN5.5 (R4.2), U9.16; also elsewhere on the board
/Input shiftreg/DI5/OUT1: RN7.8 (R1.2), U10.10; also elsewhere on the board
/Input shiftreg/DI5/OUT2: RN7.7 (R2.2), U10.12; also elsewhere on the board
/Input shiftreg/DI5/OUT3: RN7.6 (R3.2), U10.14; also elsewhere on the board
/Input shiftreg/DI5/OUT4: RN7.5 (R4.2), U10.16; also elsewhere on the board
/Input shiftreg/DI6/OUT1: RN9.8 (R1.2), U11.10; also elsewhere on the board
/Input shiftreg/DI6/OUT2: RN9.7 (R2.2), U11.12; also elsewhere on the board
/Input shiftreg/DI6/OUT3: RN9.6 (R3.2), U11.14; also elsewhere on the board
/Input shiftreg/DI6/OUT4: RN9.5 (R4.2), U11.16; also elsewhere on the board
/Input shiftreg/INA1: RN6.8 (R1.2); also elsewhere on the board
/Input shiftreg/INA2: RN6.7 (R2.2); also elsewhere on the board
/Input shiftreg/INA3: RN6.6 (R3.2); also elsewhere on the board
/Input shiftreg/INA4: RN6.5 (R4.2); also elsewhere on the board
/Input shiftreg/INA5: RN8.8 (R1.2); also elsewhere on the board
/Input shiftreg/INA6: RN8.7 (R2.2); also elsewhere on the board
/Input shiftreg/INA7: RN8.6 (R3.2); also elsewhere on the board
/Input shiftreg/INA8: RN8.5 (R4.2); also elsewhere on the board
/Input shiftreg/INB9: RN10.8 (R1.2); also elsewhere on the board
/Input shiftreg/INB10: RN10.7 (R2.2); also elsewhere on the board
/Input shiftreg/INB11: RN10.6 (R3.2); also elsewhere on the board
/Input shiftreg/INB12: RN10.5 (R4.2); also elsewhere on the board
/Input shiftreg/IN_A_COMMON: U9.2, U9.4, U9.6, U9.8, U10.2, U10.4, U10.6, U10.8; also elsewhere on the board
/Input shiftreg/IN_B_COMMON: U11.2, U11.4, U11.6, U11.8; also elsewhere on the board
GND: U9.9, U9.11, U9.13, U9.15, U10.9, U10.11, U10.13, U10.15, U11.9, U11.11, U11.13, U11.15; also elsewhere on the board
unnamed: RN6.1 (R1.1), U9.7
unnamed: RN6.2 (R2.1), U9.5
unnamed: RN6.3 (R3.1), U9.3
unnamed: RN6.4 (R4.1), U9.1
unnamed: RN8.1 (R1.1), U10.7
unnamed: RN8.2 (R2.1), U10.5
unnamed: RN8.3 (R3.1), U10.3
unnamed: RN8.4 (R4.1), U10.1
unnamed: RN10.1 (R1.1), U11.7
unnamed: RN10.2 (R2.1), U11.5
unnamed: RN10.3 (R3.1), U11.3
unnamed: RN10.4 (R4.1), U11.1


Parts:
D13: 1N4007WS; D_SOD-323F; MPN 1N4007WS; LCSC# C7528872
Q26: MMBT3906; SOT-23; MPN MMBT3906; LCSC# C727128
Q27: AO3401A; SOT-23; MPN AO3401A; LCSC# C347476
R41: 47K; R_0603_1608Metric; LCSC# C105579
R42: 10K; R_0603_1608Metric; LCSC# C98220
R43: 1R; R_0805_2012Metric; LCSC# C131397

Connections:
/Output shiftreg/DO14: D13.1 (K), Q27.3 (D); also elsewhere on the board
/Output shiftreg/DOB2/Digital output1/COLLECTOR: Q26.3 (C), Q27.1 (G), R41.2; also elsewhere on the board
/Output shiftreg/DOB2/Digital output1/EMITTER: R42.1; also elsewhere on the board
/Output shiftreg/DOB_GND: D13.2 (A), R42.2; also elsewhere on the board
/Output shiftreg/DOB_VIN: Q26.2 (E), R41.1, R43.1; also elsewhere on the board
unnamed: Q26.1 (B), Q27.2 (S), R43.2

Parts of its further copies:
D1, D2, D3, D4, D5, D6, D7, D8, D9, D10, D11, D12, D14, D15, D16: 1N4007WS; D_SOD-323F; MPN 1N4007WS; LCSC# C7528872
Q2, Q4, Q6, Q8, Q10, Q12, Q14, Q16, Q18, Q20, Q22, Q24, Q28, Q30, Q32: MMBT3906; SOT-23; MPN MMBT3906; LCSC# C727128
Q3, Q5, Q7, Q9, Q11, Q13, Q15, Q17, Q19, Q21, Q23, Q25, Q29, Q31, Q33: AO3401A; SOT-23; MPN AO3401A; LCSC# C347476
R5, R8, R11, R14, R17, R20, R23, R26, R29, R32, R35, R38, R44, R47, R50: 47K; R_0603_1608Metric; LCSC# C105579
R6, R9, R12, R15, R18, R21, R24, R27, R30, R33, R36, R39, R45, R48, R51: 10K; R_0603_1608Metric; LCSC# C98220
R7, R10, R13, R16, R19, R22, R25, R28, R31, R34, R37, R40, R46, R49, R52: 1R; R_0805_2012Metric; LCSC# C131397

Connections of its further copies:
/Output shiftreg/DO1: D1.1 (K), Q3.3 (D); also elsewhere on the board
/Output shiftreg/DO2: D2.1 (K), Q5.3 (D); also elsewhere on the board
/Output shiftreg/DO3: D3.1 (K), Q7.3 (D); also elsewhere on the board
/Output shiftreg/DO4: D4.1 (K), Q9.3 (D); also elsewhere on the board
/Output shiftreg/DO5: D7.1 (K), Q15.3 (D); also elsewhere on the board
/Output shiftreg/DO6: D8.1 (K), Q17.3 (D); also elsewhere on the board
/Output shiftreg/DO7: D5.1 (K), Q11.3 (D); also elsewhere on the board
/Output shiftreg/DO8: D6.1 (K), Q13.3 (D); also elsewhere on the board
/Output shiftreg/DO9: D12.1 (K), Q25.3 (D); also elsewhere on the board
/Output shiftreg/DO10: D9.1 (K), Q19.3 (D); also elsewhere on the board
/Output shiftreg/DO11: D11.1 (K), Q23.3 (D); also elsewhere on the board
/Output shiftreg/DO12: D10.1 (K), Q21.3 (D); also elsewhere on the board
/Output shiftreg/DO13: D16.1 (K), Q33.3 (D); also elsewhere on the board
/Output shiftreg/DO15: D15.1 (K), Q31.3 (D); also elsewhere on the board
/Output shiftreg/DO16: D14.1 (K), Q29.3 (D); also elsewhere on the board
/Output shiftreg/DOA1/Digital output1/COLLECTOR: Q4.3 (C), Q5.1 (G), R8.2; also elsewhere on the board
/Output shiftreg/DOA1/Digital output1/EMITTER: R9.1; also elsewhere on the board
/Output shiftreg/DOA1/Digital output2/COLLECTOR: Q6.3 (C), Q7.1 (G), R11.2; also elsewhere on the board
/Output shiftreg/DOA1/Digital output2/EMITTER: R12.1; also elsewhere on the board
/Output shiftreg/DOA1/Digital output3/COLLECTOR: Q8.3 (C), Q9.1 (G), R14.2; also elsewhere on the board
/Output shiftreg/DOA1/Digital output3/EMITTER: R15.1; also elsewhere on the board
/Output shiftreg/DOA1/Digital output/COLLECTOR: Q2.3 (C), Q3.1 (G), R5.2; also elsewhere on the board
/Output shiftreg/DOA1/Digital output/EMITTER: R6.1; also elsewhere on the board
/Output shiftreg/DOA2/Digital output1/COLLECTOR: Q16.3 (C), Q17.1 (G), R26.2; also elsewhere on the board
/Output shiftreg/DOA2/Digital output1/EMITTER: R27.1; also elsewhere on the board
/Output shiftreg/DOA2/Digital output2/COLLECTOR: Q10.3 (C), Q11.1 (G), R17.2; also elsewhere on the board
/Output shiftreg/DOA2/Digital output2/EMITTER: R18.1; also elsewhere on the board
/Output shiftreg/DOA2/Digital output3/COLLECTOR: Q12.3 (C), Q13.1 (G), R20.2; also elsewhere on the board
/Output shiftreg/DOA2/Digital output3/EMITTER: R21.1; also elsewhere on the board
/Output shiftreg/DOA2/Digital output/COLLECTOR: Q14.3 (C), Q15.1 (G), R23.2; also elsewhere on the board
/Output shiftreg/DOA2/Digital output/EMITTER: R24.1; also elsewhere on the board
/Output shiftreg/DOA_GND: D1.2 (A), D2.2 (A), D3.2 (A), D4.2 (A), D5.2 (A), D6.2 (A), D7.2 (A), D8.2 (A), R6.2, R9.2, R12.2, R15.2, R18.2, R21.2, R24.2, R27.2; also elsewhere on the board
/Output shiftreg/DOA_VIN: Q2.2 (E), Q4.2 (E), Q6.2 (E), Q8.2 (E), Q10.2 (E), Q12.2 (E), Q14.2 (E), Q16.2 (E), R5.1, R7.1, R8.1, R10.1, R11.1, R13.1, R14.1, R16.1, R17.1, R19.1, R20.1, R22.1, R23.1, R25.1, R26.1, R28.1; also elsewhere on the board
/Output shiftreg/DOB1/Digital output1/COLLECTOR: Q18.3 (C), Q19.1 (G), R29.2; also elsewhere on the board
/Output shiftreg/DOB1/Digital output1/EMITTER: R30.1; also elsewhere on the board
/Output shiftreg/DOB1/Digital output2/COLLECTOR: Q22.3 (C), Q23.1 (G), R35.2; also elsewhere on the board
/Output shiftreg/DOB1/Digital output2/EMITTER: R36.1; also elsewhere on the board
/Output shiftreg/DOB1/Digital output3/COLLECTOR: Q20.3 (C), Q21.1 (G), R32.2; also elsewhere on the board
/Output shiftreg/DOB1/Digital output3/EMITTER: R33.1; also elsewhere on the board
/Output shiftreg/DOB1/Digital output/COLLECTOR: Q24.3 (C), Q25.1 (G), R38.2; also elsewhere on the board
/Output shiftreg/DOB1/Digital output/EMITTER: R39.1; also elsewhere on the board
/Output shiftreg/DOB2/Digital output2/COLLECTOR: Q30.3 (C), Q31.1 (G), R47.2; also elsewhere on the board
/Output shiftreg/DOB2/Digital output2/EMITTER: R48.1; also elsewhere on the board
/Output shiftreg/DOB2/Digital output3/COLLECTOR: Q28.3 (C), Q29.1 (G), R44.2; also elsewhere on the board
/Output shiftreg/DOB2/Digital output3/EMITTER: R45.1; also elsewhere on the board
/Output shiftreg/DOB2/Digital output/COLLECTOR: Q32.3 (C), Q33.1 (G), R50.2; also elsewhere on the board
/Output shiftreg/DOB2/Digital output/EMITTER: R51.1; also elsewhere on the board
/Output shiftreg/DOB_GND: D9.2 (A), D10.2 (A), D11.2 (A), D12.2 (A), D14.2 (A), D15.2 (A), D16.2 (A), R30.2, R33.2, R36.2, R39.2, R45.2, R48.2, R51.2; also elsewhere on the board
/Output shiftreg/DOB_VIN: Q18.2 (E), Q20.2 (E), Q22.2 (E), Q24.2 (E), Q28.2 (E), Q30.2 (E), Q32.2 (E), R29.1, R31.1, R32.1, R34.1, R35.1, R37.1, R38.1, R40.1, R44.1, R46.1, R47.1, R49.1, R50.1, R52.1; also elsewhere on the board
unnamed: Q2.1 (B), Q3.2 (S), R7.2
unnamed: Q4.1 (B), Q5.2 (S), R10.2
unnamed: Q6.1 (B), Q7.2 (S), R13.2
unnamed: Q8.1 (B), Q9.2 (S), R16.2
unnamed: Q10.1 (B), Q11.2 (S), R19.2
unnamed: Q12.1 (B), Q13.2 (S), R22.2
unnamed: Q14.1 (B), Q15.2 (S), R25.2
unnamed: Q16.1 (B), Q17.2 (S), R28.2
unnamed: Q18.1 (B), Q19.2 (S), R31.2
unnamed: Q20.1 (B), Q21.2 (S), R34.2
unnamed: Q22.1 (B), Q23.2 (S), R37.2
unnamed: Q24.1 (B), Q25.2 (S), R40.2
unnamed: Q28.1 (B), Q29.2 (S), R46.2
unnamed: Q30.1 (B), Q31.2 (S), R49.2
unnamed: Q32.1 (B), Q33.2 (S), R52.2

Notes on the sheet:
Current limited PNP output at ~0.6A


Board: 2 copper layers, 100.0 x 100.0 mm, 141 parts (0 on the bottom side), 170 nets.

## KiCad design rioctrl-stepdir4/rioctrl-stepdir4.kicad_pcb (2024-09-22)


Board: 2 copper layers, 100.0 x 100.0 mm, 98 parts (0 on the bottom side), 84 nets.

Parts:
C1, C2: 10uF; C_0805_2012Metric
C3, C4, C5, C6, C7, C8, C9, C10: 0.1uF; C_0603_1608Metric
D1, D3, D6, D9, D12: BZT52C10S; D_SOD-323
D2, D4, D7, D10, D13: SMF24A; D_SOD-123F
F1, F2, F3, F4: BSMD1206-100-24V; Fuse_1206_3216Metric
FB1, FB2, FB3, FB4: FB_100R_3A; L_0603_1608Metric
H1, H2, H3, H4: MH_3.2mm; MountingHole_3.2mm_M3_Pad_Via
J1: Conn_02x13_Odd_Even; PinHeader_2x13_P2.54mm_Horizontal
J2, J3, J4, J5: RJ45_LED_Shielded; R-RJ45R08P-C000
Q1, Q2, Q5, Q7, Q9, Q11: BSS138W; SOT-323_SC-70
Q3, Q4, Q6, Q8, Q10, Q12: AO3401A; SOT-23
R1, R2, R3, R4, R5, R6, R7, R12, R13, R14, R15, R20, R21, R22, R23, R28, R29, R30, R31, R36, R37: 10K; R_0603_1608Metric
R8, R9, R10, R11, R16, R17, R18, R19, R24, R25, R26, R27, R32, R33, R34, R35: 100R; R_0603_1608Metric
U1, U2, U4, U5, U7, U8, U10, U11: CS48505S; SOIC-8_3.9x4.9mm_P1.27mm
U3, U6, U9, U12: USBLC6-4SC6; SOT-23-6

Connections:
+3V3: J1.17, J1.18
+5V: J1.19, J1.20, Q4.2 (S), R4.1, U3.5 (VBUS), U6.5 (VBUS), U9.5 (VBUS), U12.5 (VBUS)
+5V_EN: C2.1, FB1.1, FB2.1, FB3.1, FB4.1, Q4.3 (D)
+24V: D1.1 (K), J1.21, J1.22, Q3.2 (S), R3.1
+24V_EN: C1.1, D2.1 (A1), D3.1 (K), D6.1 (K), D9.1 (K), D12.1 (K), Q3.3 (D), Q6.2 (S), Q8.2 (S), Q10.2 (S), Q12.2 (S), R6.1, R14.1, R22.1, R30.1
/Slot input/S0: J1.3, U1.4 (DI)
/Slot input/S1: J1.5, U2.4 (DI)
/Slot input/S2: J1.7, R5.2
/Slot input/S3: J1.9, U4.4 (DI)
/Slot input/S4: J1.11, U5.4 (DI)
/Slot input/S5: J1.13, R13.2
/Slot input/S6: J1.4, U7.4 (DI)
/Slot input/S7: J1.6, U8.4 (DI)
/Slot input/S8: J1.8, R21.2
/Slot input/S9: J1.10, U10.4 (DI)
/Slot input/S10: J1.12, U11.4 (DI)
/Slot input/S11: J1.14, R29.2
/Slot input/SlotEN: J1.23, J1.24, R1.2, R2.2
/Step dir output 1/DIR_OUT_N: R33.1, U11.7 (B), U12.4 (I/O3)
/Step dir output 1/DIR_OUT_P: R32.1, U11.6 (A), U12.6 (I/O4)
/Step dir output 1/DIR_OUT_P_N: J5.6, R33.2
/Step dir output 1/DIR_OUT_P_P: J5.3, R32.2
/Step dir output 1/EN_OUT: F4.2, J5.4, J5.10
/Step dir output 1/STEP_OUT_N: R35.1, U10.7 (B), U12.1 (I/O1)
/Step dir output 1/STEP_OUT_P: R34.1, U10.6 (A), U12.3 (I/O2)
/Step dir output 1/STEP_OUT_P_N: J5.2, R35.2
/Step dir output 1/STEP_OUT_P_P: J5.1, R34.2
/Step dir output 2/DIR_OUT_N: R25.1, U8.7 (B), U9.4 (I/O3)
/Step dir output 2/DIR_OUT_P: R24.1, U8.6 (A), U9.6 (I/O4)
/Step dir output 2/DIR_OUT_P_N: J4.6, R25.2
/Step dir output 2/DIR_OUT_P_P: J4.3, R24.2
/Step dir output 2/EN_OUT: F3.2, J4.4, J4.10
/Step dir output 2/STEP_OUT_N: R27.1, U7.7 (B), U9.1 (I/O1)
/Step dir output 2/STEP_OUT_P: R26.1, U7.6 (A), U9.3 (I/O2)
/Step dir output 2/STEP_OUT_P_N: J4.2, R27.2
/Step dir output 2/STEP_OUT_P_P: J4.1, R26.2
/Step dir output 3/DIR_OUT_N: R17.1, U5.7 (B), U6.4 (I/O3)
/Step dir output 3/DIR_OUT_P: R16.1, U5.6 (A), U6.6 (I/O4)
/Step dir output 3/DIR_OUT_P_N: J3.6, R17.2
/Step dir output 3/DIR_OUT_P_P: J3.3, R16.2
/Step dir output 3/EN_OUT: F2.2, J3.4, J3.10
/Step dir output 3/STEP_OUT_N: R19.1, U4.7 (B), U6.1 (I/O1)
/Step dir output 3/STEP_OUT_P: R18.1, U4.6 (A), U6.3 (I/O2)
/Step dir output 3/STEP_OUT_P_N: J3.2, R19.2
/Step dir output 3/STEP_OUT_P_P: J3.1, R18.2
/Step dir output 4/DIR_OUT_N: R9.1, U2.7 (B), U3.4 (I/O3)
/Step dir output 4/DIR_OUT_P: R8.1, U2.6 (A), U3.6 (I/O4)
/Step dir output 4/DIR_OUT_P_N: J2.6, R9.2
/Step dir output 4/DIR_OUT_P_P: J2.3, R8.2
/Step dir output 4/EN_OUT: F1.2, J2.4, J2.10
/Step dir output 4/STEP_OUT_N: R11.1, U1.7 (B), U3.1 (I/O1)
/Step dir output 4/STEP_OUT_P: R10.1, U1.6 (A), U3.3 (I/O2)
/Step dir output 4/STEP_OUT_P_N: J2.2, R11.2
/Step dir output 4/STEP_OUT_P_P: J2.1, R10.2
GND: C1.2, C2.2, C3.2, C4.2, C5.2, C6.2, C7.2, C8.2, C9.2, C10.2, D2.2 (A2), D4.2 (A2), D7.2 (A2), D10.2 (A2), D13.2 (A2), H1.1, H2.1, H3.1, H4.1, J1.1, J1.2, J1.15, J1.16, J1.25, J1.26, J2.5, J2.7, J2.8, J2.SH, J3.5, J3.7, J3.8, J3.SH, J4.5, J4.7, J4.8, J4.SH, J5.5, J5.7, J5.8, J5.SH, Q1.2 (S), Q2.2 (S), Q5.2 (S), Q7.2 (S), Q9.2 (S), Q11.2 (S), R12.2, R20.2, R28.2, R36.2, U1.5 (GND), U2.5 (GND), U3.2 (GND), U4.5 (GND), U5.5 (GND), U6.2 (GND), U7.5 (GND), U8.5 (GND), U9.2 (GND), U10.5 (GND), U11.5 (GND), U12.2 (GND)
unnamed: D1.2 (A), Q3.1 (G), R3.2, R7.1
unnamed: D3.2 (A), Q6.1 (G), R6.2, R15.1
unnamed: D4.1 (A1), F1.1, Q6.3 (D)
unnamed: D6.2 (A), Q8.1 (G), R14.2, R23.1
unnamed: D7.1 (A1), F2.1, Q8.3 (D)
unnamed: D9.2 (A), Q10.1 (G), R22.2, R31.1
unnamed: D10.1 (A1), F3.1, Q10.3 (D)
unnamed: D12.2 (A), Q12.1 (G), R30.2, R37.1
unnamed: D13.1 (A1), F4.1, Q12.3 (D)
unnamed: J2.9, R12.1
unnamed: J3.9, R20.1
unnamed: J4.9, R28.1
unnamed: J5.9, R36.1
unnamed: Q1.3 (D), R7.2
unnamed: Q1.1 (G), R1.1
unnamed: Q2.3 (D), Q4.1 (G), R4.2
unnamed: Q2.1 (G), R2.1
unnamed: Q5.3 (D), R15.2
unnamed: Q5.1 (G), R5.1
unnamed: Q7.3 (D), R23.2
unnamed: Q7.1 (G), R13.1
unnamed: Q9.3 (D), R31.2
unnamed: Q9.1 (G), R21.1
unnamed: Q11.3 (D), R37.2
unnamed: Q11.1 (G), R29.1
unnamed: C3.1, C4.1, FB1.2, U1.2 (~RE), U1.3 (DE), U1.8 (VCC), U2.2 (~RE), U2.3 (DE), U2.8 (VCC)
unnamed: C5.1, C6.1, FB2.2, U4.2 (~RE), U4.3 (DE), U4.8 (VCC), U5.2 (~RE), U5.3 (DE), U5.8 (VCC)
unnamed: C7.1, C8.1, FB3.2, U7.2 (~RE), U7.3 (DE), U7.8 (VCC), U8.2 (~RE), U8.3 (DE), U8.8 (VCC)
unnamed: C9.1, C10.1, FB4.2, U10.2 (~RE), U10.3 (DE), U10.8 (VCC), U11.2 (~RE), U11.3 (DE), U11.8 (VCC)

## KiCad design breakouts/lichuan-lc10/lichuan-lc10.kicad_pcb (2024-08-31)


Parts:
J1, J2: RJ45_LED_Shielded; R-RJ45R08P-C000; MPN R-RJ45R08P-C000; LCSC# C386757
J3: TERM-BLK-8H-S; MX250-3.5-08P-B; MPN MX250-3.5-08P-B-GY01-Cu-A; LCSC# C7470122
J4: Conn_01x03; PinHeader_1x03_P2.54mm_Vertical
J5: Conn_01x02; PinHeader_1x02_P2.54mm_Vertical
JP1, JP2, JP3: SolderJumper_2_Open; SolderJumper-2_P1.3mm_Open_RoundedPad1.0x1.5mm; not fitted
U1: DSUB-44-HD_Male_Horizontal_P2.29x1.98mm_EdgePinOffset8.35mm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; MPN DS1038-44MBNSIA74-0CC; LCSC# C77845

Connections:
/+24VO: J5.1, U1.44 (+24VO)
/AGND: J4.3, U1.16 (AGND), U1.18 (AGND)
/AI1: J4.1, U1.19 (AI1)
/AI2: J4.2, U1.17 (AI2)
/COM-: J5.2, U1.11 (COM-), U1.12 (COM-)
/DIR_N: J1.6, U1.39 (DIR-)
/DIR_P: J1.3, U1.40 (DIR+)
/DI_COM: J3.2, U1.10 (DICOM)
/DI_ESTOP: J3.7, U1.32 (DI6/ESTOP)
/DI_SON: J3.3, U1.24 (DI1/SON)
/DO_BRAKE: J3.1, U1.27 (DO6A/BRAKE)
/DO_COM: J3.6, U1.1 (DOxB), U1.3 (DO3B), U1.5 (DO2B), U1.7 (DO1B), U1.9 (DO5B), U1.26 (DO6B)
/DO_FAULT: J3.8, U1.2 (DO4A/FAULT)
/DO_IN_POS: J3.5, U1.6 (DO2A/IN_POS)
/DO_RDY: J3.4, U1.8 (DO1A/RDY)
/ENC_A_N: J2.2, U1.13 (OA-)
/ENC_A_P: J2.1, U1.28 (OA+)
/ENC_B_N: J2.6, U1.14 (OB-)
/ENC_B_P: J2.3, U1.29 (OB+)
/ENC_GND: J2.8, JP3.2 (B), U1.20 (GND)
/ENC_Z_N: J2.5, U1.15 (OZ-)
/ENC_Z_P: J2.4, U1.30 (OZ+)
/SD_GND: J1.8, JP1.2 (B), JP2.2 (B)
/STEP_N: J1.2, U1.41 (PUL-)
/STEP_P: J1.1, U1.42 (PUL+)
unnamed: J1.SH, JP1.1 (A)
unnamed: JP2.1 (A), U1.38 (OPC)
unnamed: J2.SH, JP3.1 (A)

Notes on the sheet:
Digital outputs are NPN



Board: 2 copper layers, 40.5 x 78.0 mm, 9 parts (3 on the bottom side), 28 nets.

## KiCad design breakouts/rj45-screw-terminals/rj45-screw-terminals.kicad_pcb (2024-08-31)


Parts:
H3, H4: MH_3.2mm; MountingHole_3.2mm_M3_Pad_Via; not fitted
J1: RJ45_LED_Shielded; R-RJ45R08P-C000; MPN R-RJ45R08P-C000; LCSC# C386757
J2: Conn_01x02; PinHeader_1x02_P2.54mm_Vertical
J3: TERM-BLK-8H-S; MX250-3.5-08P-B; MPN MX250-3.5-08P-B-GY01-Cu-A; LCSC# C7470122

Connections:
GND: J1.8, J2.2, J3.8
unnamed: J1.SH, J2.1
unnamed: J1.1, J3.1
unnamed: J1.2, J3.2
unnamed: J1.3, J3.3
unnamed: J1.4, J3.4
unnamed: J1.5, J3.5
unnamed: J1.6, J3.6
unnamed: J1.7, J3.7


Board: 2 copper layers, 34.0 x 37.0 mm, 5 parts (0 on the bottom side), 9 nets.

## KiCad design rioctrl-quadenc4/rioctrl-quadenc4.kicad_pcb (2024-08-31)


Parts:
C1, C2, C3: 0.1uF; C_0603_1608Metric; LCSC# C14663
C4: 10uF; C_0805_2012Metric; MPN GRM21BR61H106KE43L; LCSC# C440198
D1: BSD5C031V; D_SOD-523; MPN BSD5C031V; LCSC# C151984
D2: PESD5V0S1BBN; D_SOD-523; MPN PESD5V0S1BBN; LCSC# C314264
FB1: FB_100R_3A; L_0603_1608Metric; MPN UPZ1608E101-3R0TF; LCSC# C96995
J1: RJ45_LED_Shielded; R-RJ45R08P-C000; MPN R-RJ45R08P-C000; LCSC# C386757
R1, R3, R4, R6, R7, R9: 1K; R_0603_1608Metric; LCSC# C22548
R2, R5, R8: 120R; R_0603_1608Metric; LCSC# C114640
R10, R11, R12, R13, R14, R15: 10R; R_0603_1608Metric; LCSC# C109318
R16: 0R; R_0603_1608Metric; LCSC# C95177
U1, U2, U3: CS48505S; SOIC-8_3.9x4.9mm_P1.27mm; MPN CS48505S; LCSC# C3202824
U4, U5: USBLC6-4SC6; SOT-23-6; MPN USBLC6-4SC6; LCSC# C5197386

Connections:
+3V3: C1.1, C2.1, C3.1, D1.1 (A1), R1.1, R4.1, R7.1, U1.8 (VCC), U2.8 (VCC), U3.8 (VCC), U4.5 (VBUS), U5.5 (VBUS); also elsewhere on the board
+5V: C4.1, D2.2 (A2), FB1.1; also elsewhere on the board
/Quadenc/A: U3.1 (RO); also elsewhere on the board
/Quadenc/A_IN_N: R8.1, R9.1, R11.1, U3.7 (B), U4.1 (I/O1)
/Quadenc/A_IN_P: R7.2, R8.2, R10.1, U3.6 (A), U4.3 (I/O2)
/Quadenc/B: U1.1 (RO); also elsewhere on the board
/Quadenc/B_IN_N: R2.2, R3.1, R15.1, U1.7 (B), U4.4 (I/O3)
/Quadenc/B_IN_P: R1.2, R2.1, R12.1, U1.6 (A), U4.6 (I/O4)
/Quadenc/Z: U2.1 (RO); also elsewhere on the board
/Quadenc/Z_IN_N: R5.2, R6.1, R14.1, U2.7 (B), U5.4 (I/O3)
/Quadenc/Z_IN_P: R4.2, R5.1, R13.1, U2.6 (A), U5.6 (I/O4)
GND: C1.2, C2.2, C3.2, C4.2, D1.2 (A2), D2.1 (A1), J1.8, R3.2, R6.2, R9.2, R16.2, U1.2 (~RE), U1.3 (DE), U1.5 (GND), U2.2 (~RE), U2.3 (DE), U2.5 (GND), U3.2 (~RE), U3.3 (DE), U3.5 (GND), U4.2 (GND), U5.2 (GND); also elsewhere on the board
unnamed: FB1.2, J1.7
unnamed: J1.1, R10.2
unnamed: J1.2, R11.2
unnamed: J1.3, R12.2
unnamed: J1.4, R13.2
unnamed: J1.5, R14.2
unnamed: J1.6, R15.2
unnamed: J1.SH, R16.1

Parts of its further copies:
C5, C6, C7, C9, C10, C11, C13, C14, C15: 0.1uF; C_0603_1608Metric; LCSC# C14663
C8, C12, C16: 10uF; C_0805_2012Metric; MPN GRM21BR61H106KE43L; LCSC# C440198
D3, D5, D7: BSD5C031V; D_SOD-523; MPN BSD5C031V; LCSC# C151984
D4, D6, D8: PESD5V0S1BBN; D_SOD-523; MPN PESD5V0S1BBN; LCSC# C314264
FB2, FB3, FB4: FB_100R_3A; L_0603_1608Metric; MPN UPZ1608E101-3R0TF; LCSC# C96995
J3, J4, J5: RJ45_LED_Shielded; R-RJ45R08P-C000; MPN R-RJ45R08P-C000; LCSC# C386757
R17, R19, R20, R22, R23, R25, R33, R35, R36, R38, R39, R41, R49, R51, R52, R54, R55, R57: 1K; R_0603_1608Metric; LCSC# C22548
R18, R21, R24, R34, R37, R40, R50, R53, R56: 120R; R_0603_1608Metric; LCSC# C114640
R26, R27, R28, R29, R30, R31, R42, R43, R44, R45, R46, R47, R58, R59, R60, R61, R62, R63: 10R; R_0603_1608Metric; LCSC# C109318
R32, R48, R64: 0R; R_0603_1608Metric; LCSC# C95177
U6, U7, U8, U11, U12, U13, U16, U17, U18: CS48505S; SOIC-8_3.9x4.9mm_P1.27mm; MPN CS48505S; LCSC# C3202824
U9, U10, U14, U15, U19, U20: USBLC6-4SC6; SOT-23-6; MPN USBLC6-4SC6; LCSC# C5197386

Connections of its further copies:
+3V3: C5.1, C6.1, C7.1, C9.1, C10.1, C11.1, C13.1, C14.1, C15.1, D3.1 (A1), D5.1 (A1), D7.1 (A1), R17.1, R20.1, R23.1, R33.1, R36.1, R39.1, R49.1, R52.1, R55.1, U6.8 (VCC), U7.8 (VCC), U8.8 (VCC), U9.5 (VBUS), U10.5 (VBUS), U11.8 (VCC), U12.8 (VCC), U13.8 (VCC), U14.5 (VBUS), U15.5 (VBUS), U16.8 (VCC), U17.8 (VCC), U18.8 (VCC), U19.5 (VBUS), U20.5 (VBUS); also elsewhere on the board
+5V: C8.1, C12.1, C16.1, D4.2 (A2), D6.2 (A2), D8.2 (A2), FB2.1, FB3.1, FB4.1; also elsewhere on the board
/Quadenc1/A: U8.1 (RO); also elsewhere on the board
/Quadenc1/A_IN_N: R24.1, R25.1, R27.1, U8.7 (B), U9.1 (I/O1)
/Quadenc1/A_IN_P: R23.2, R24.2, R26.1, U8.6 (A), U9.3 (I/O2)
/Quadenc1/B: U6.1 (RO); also elsewhere on the board
/Quadenc1/B_IN_N: R18.2, R19.1, R31.1, U6.7 (B), U9.4 (I/O3)
/Quadenc1/B_IN_P: R17.2, R18.1, R28.1, U6.6 (A), U9.6 (I/O4)
/Quadenc1/Z: U7.1 (RO); also elsewhere on the board
/Quadenc1/Z_IN_N: R21.2, R22.1, R30.1, U7.7 (B), U10.4 (I/O3)
/Quadenc1/Z_IN_P: R20.2, R21.1, R29.1, U7.6 (A), U10.6 (I/O4)
/Quadenc2/A: U13.1 (RO); also elsewhere on the board
/Quadenc2/A_IN_N: R40.1, R41.1, R43.1, U13.7 (B), U14.1 (I/O1)
/Quadenc2/A_IN_P: R39.2, R40.2, R42.1, U13.6 (A), U14.3 (I/O2)
/Quadenc2/B: U11.1 (RO); also elsewhere on the board
/Quadenc2/B_IN_N: R34.2, R35.1, R47.1, U11.7 (B), U14.4 (I/O3)
/Quadenc2/B_IN_P: R33.2, R34.1, R44.1, U11.6 (A), U14.6 (I/O4)
/Quadenc2/Z: U12.1 (RO); also elsewhere on the board
/Quadenc2/Z_IN_N: R37.2, R38.1, R46.1, U12.7 (B), U15.4 (I/O3)
/Quadenc2/Z_IN_P: R36.2, R37.1, R45.1, U12.6 (A), U15.6 (I/O4)
/Quadenc3/A: U18.1 (RO); also elsewhere on the board
/Quadenc3/A_IN_N: R56.1, R57.1, R59.1, U18.7 (B), U19.1 (I/O1)
/Quadenc3/A_IN_P: R55.2, R56.2, R58.1, U18.6 (A), U19.3 (I/O2)
/Quadenc3/B: U16.1 (RO); also elsewhere on the board
/Quadenc3/B_IN_N: R50.2, R51.1, R63.1, U16.7 (B), U19.4 (I/O3)
/Quadenc3/B_IN_P: R49.2, R50.1, R60.1, U16.6 (A), U19.6 (I/O4)
/Quadenc3/Z: U17.1 (RO); also elsewhere on the board
/Quadenc3/Z_IN_N: R53.2, R54.1, R62.1, U17.7 (B), U20.4 (I/O3)
/Quadenc3/Z_IN_P: R52.2, R53.1, R61.1, U17.6 (A), U20.6 (I/O4)
GND: C5.2, C6.2, C7.2, C8.2, C9.2, C10.2, C11.2, C12.2, C13.2, C14.2, C15.2, C16.2, D3.2 (A2), D4.1 (A1), D5.2 (A2), D6.1 (A1), D7.2 (A2), D8.1 (A1), J3.8, J4.8, J5.8, R19.2, R22.2, R25.2, R32.2, R35.2, R38.2, R41.2, R48.2, R51.2, R54.2, R57.2, R64.2, U6.2 (~RE), U6.3 (DE), U6.5 (GND), U7.2 (~RE), U7.3 (DE), U7.5 (GND), U8.2 (~RE), U8.3 (DE), U8.5 (GND), U9.2 (GND), U10.2 (GND), U11.2 (~RE), U11.3 (DE), U11.5 (GND), U12.2 (~RE), U12.3 (DE), U12.5 (GND), U13.2 (~RE), U13.3 (DE), U13.5 (GND), U14.2 (GND), U15.2 (GND), U16.2 (~RE), U16.3 (DE), U16.5 (GND), U17.2 (~RE), U17.3 (DE), U17.5 (GND), U18.2 (~RE), U18.3 (DE), U18.5 (GND), U19.2 (GND), U20.2 (GND); also elsewhere on the board
unnamed: FB2.2, J3.7
unnamed: FB3.2, J4.7
unnamed: FB4.2, J5.7
unnamed: J3.1, R26.2
unnamed: J3.2, R27.2
unnamed: J3.3, R28.2
unnamed: J3.4, R29.2
unnamed: J3.5, R30.2
unnamed: J3.6, R31.2
unnamed: J3.SH, R32.1
unnamed: J4.1, R42.2
unnamed: J4.2, R43.2
unnamed: J4.3, R44.2
unnamed: J4.4, R45.2
unnamed: J4.5, R46.2
unnamed: J4.6, R47.2
unnamed: J4.SH, R48.1
unnamed: J5.1, R58.2
unnamed: J5.2, R59.2
unnamed: J5.3, R60.2
unnamed: J5.4, R61.2
unnamed: J5.5, R62.2
unnamed: J5.6, R63.2
unnamed: J5.SH, R64.1


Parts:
H1, H2, H3, H4: MH_3.2mm; MountingHole_3.2mm_M3_Pad_Via; not fitted
J2: Conn_02x13_Odd_Even; PinHeader_2x13_P2.54mm_Horizontal; LCSC# C2894993

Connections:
+3V3: J2.17, J2.18; also elsewhere on the board
+5V: J2.19, J2.20; also elsewhere on the board
+24V: J2.21, J2.22
/Quadenc1/A: J2.13; also elsewhere on the board
/Quadenc1/B: J2.11; also elsewhere on the board
/Quadenc1/Z: J2.9; also elsewhere on the board
/Quadenc2/A: J2.8; also elsewhere on the board
/Quadenc2/B: J2.6; also elsewhere on the board
/Quadenc2/Z: J2.4; also elsewhere on the board
/Quadenc3/A: J2.14; also elsewhere on the board
/Quadenc3/B: J2.12; also elsewhere on the board
/Quadenc3/Z: J2.10; also elsewhere on the board
/Quadenc/A: J2.7; also elsewhere on the board
/Quadenc/B: J2.5; also elsewhere on the board
/Quadenc/Z: J2.3; also elsewhere on the board
/Slot/SlotEN: J2.23, J2.24
GND: H1.1, H2.1, H3.1, H4.1, J2.1, J2.2, J2.15, J2.16, J2.25, J2.26; also elsewhere on the board


Board: 2 copper layers, 100.0 x 100.0 mm, 121 parts (0 on the bottom side), 73 nets.

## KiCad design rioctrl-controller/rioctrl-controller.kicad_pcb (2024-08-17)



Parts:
C47, C48, C49, C50, C51, C52, C53, C54, C56, C57, C58, C59, C60, C61, C62, C63, C64, C65, C66, C67: 0.1uF; C_0402_1005Metric
C55: 0.1uF; C_0603_1608Metric; MPN CC0603KRX7R9BB104; LCSC# C14663
D10, D12: LED_RED; LED_0603_1608Metric; MPN SZYY0603R; LCSC# C434419
D11: LED_GREEN; LED_0603_1608Metric; MPN SZYY0603YG; LCSC# C434423
J8: Conn_02x05_PH; IDC-Header_2x05_P2.54mm_Vertical
J10: Conn_02x06_Odd_Even; PinSocket_2x06_P2.54mm_Horizontal
Q1, Q2, Q3: BSS138W; SOT-323_SC-70; MPN BSS138W; LCSC# C504052
R44, R45, R46, R48, R49: 10K; R_0603_1608Metric
R47: 10K; R_0603_1608Metric; MPN RC0603FR-0710KL; LCSC# C98220
R50, R51, R52: 330R; R_0603_1608Metric
U9: ECP5U_45_CABGA256; BGA-256_14.0x14.0mm_Layout16x16_P0.8mm_Ball0.45mm_Pad0.32mm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; MPN LFE5U-12F-6BG256C
U10: W25Q16JVSS; SOIC-8_5.23x5.23mm_P1.27mm; MPN W25Q16JVSSIQ; LCSC# C82317
X1: OSC_25MHz; Oscillator_SMD_EuroQuartz_XO32-4Pin_3.2x2.5mm; MPN OT322525MJBA4SL; LCSC# C669088

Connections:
+1V1: C47.1, C48.1, C49.1, C50.1, U9.G6 (VCC[6]), U9.G7 (VCC[6]), U9.G9 (VCC[6]), U9.L8 (VCC[6]), U9.L9 (VCC[6]), U9.L10 (VCC[6]); also elsewhere on the board
+2V5: C51.1, C52.1, U9.G11 (VCCAUX[2]), U9.L7 (VCCAUX[2]); also elsewhere on the board
+3V3: C53.1, C54.1, C55.1, C56.1, C57.1, C58.1, C59.1, C60.1, C61.1, C62.1, C63.1, C64.1, C65.1, C66.1, C67.1, J8.1, J10.1, J10.2, R46.1, R47.2, R48.1, R50.1, R51.1, R52.1, U9.F6 (VCCIO0[2]), U9.F7 (VCCIO0[2]), U9.F10 (VCCIO1[2]), U9.F11 (VCCIO1[2]), U9.H6 (VCCIO7[2]), U9.H7 (VCCIO7[2]), U9.H11 (VCCIO2[2]), U9.J6 (VCCIO6[2]), U9.J7 (VCCIO6[2]), U9.J11 (VCCIO2[2]), U9.K11 (VCCIO3[2]), U9.L6 (VCCIO8), U9.L11 (VCCIO3[2]), U10.8 (VCC), X1.4 (V+); also elsewhere on the board
/FPGA/CFG_1: R46.2, U9.P10 (CFG_1)
/FPGA/CFG_2: R45.1, U9.R10 (CFG_2)
/FPGA/DONE: Q2.1 (G), U9.P9 (DONE)
/FPGA/FLASH_CLK: U9.N9 (CCLK/MCLK/SCK), U10.6 (CLK)
/FPGA/FLASH_CS: R47.1, U9.N8 (PB15A/+/HOLDN/DI/BUSY/CSSPIN/CEN), U10.1 (~CS)
/FPGA/FLASH_DI: U9.T8 (PB11B/-/D0/MOSI/IO0), U10.5 (DI(IO0))
/FPGA/FLASH_DO: U9.T7 (PB11A/+/D1/MISO/IO1), U10.2 (DO(IO1))
/FPGA/FLASH_IO2: U9.M7 (PB9B/-/D2/IO2), U10.3 (IO2)
/FPGA/FLASH_IO3: U9.N7 (PB9A/+/D3/IO3), U10.7 (IO3)
/FPGA/LED_ERR: Q1.1 (G), U9.L1 (PL35A/+/PCLKT6_1/HS/LDQ41)
/FPGA/LED_OK: Q3.1 (G), U9.N1 (PL41A/+/HS/LDQS41)
/FPGA/MCLK: U9.A7 (PT38A/+/PCLKT0_0), X1.3 (OUT)
/FPGA/PMOD_P1: J10.11, U9.A2 (PT4A/+/ULC_GPLL1T_IN)
/FPGA/PMOD_P2: J10.9, U9.A3 (PT6A/+)
/FPGA/PMOD_P3: J10.7, U9.E2 (PL17B/-/HS/LDQSN17)
/FPGA/PMOD_P4: J10.5, U9.C2 (PL14B/-/HS/LDQ17)
/FPGA/PMOD_P7: J10.12, U9.B2 (PL11B/-/ULC_GPLL0C_IN/HS/LDQ17)
/FPGA/PMOD_P8: J10.10, U9.B3 (PT4B/-/ULC_GPLL1C_IN)
/FPGA/PMOD_P9: J10.8, U9.F3 (PL14D/-/LDQ17)
/FPGA/PMOD_P10: J10.6, U9.C3 (PL11C/+/LDQ17)
/FPGA/SA0: U9.A4 (PT6B/-); also elsewhere on the board
/FPGA/SA1: U9.B4 (PT11B/-); also elsewhere on the board
/FPGA/SA2: U9.C4 (PT11A/+); also elsewhere on the board
/FPGA/SA3: U9.D4 (PT9B/-); also elsewhere on the board
/FPGA/SA4: U9.E4 (PT9A/+); also elsewhere on the board
/FPGA/SA5: U9.B5 (PT15B/-); also elsewhere on the board
/FPGA/SA6: U9.C5 (PT15A/+); also elsewhere on the board
/FPGA/SA7: U9.D5 (PT13B/-); also elsewhere on the board
/FPGA/SA8: U9.E5 (PT13A/+); also elsewhere on the board
/FPGA/SA9: U9.A5 (PT18A/+); also elsewhere on the board
/FPGA/SB0: U9.A6 (PT18B/-); also elsewhere on the board
/FPGA/SB1: U9.B6 (PT31B/-); also elsewhere on the board
/FPGA/SB2: U9.C6 (PT31A/+); also elsewhere on the board
/FPGA/SB3: U9.D6 (PT20B/-); also elsewhere on the board
/FPGA/SB4: U9.B7 (PT36B/-/PCLKC0_1); also elsewhere on the board
/FPGA/SB5: U9.C7 (PT36A/+/PCLKT0_1); also elsewhere on the board
/FPGA/SB6: U9.D7 (PT33B/-/GR_PCLK0_0); also elsewhere on the board
/FPGA/SB7: U9.A8 (PT38B/-/PCLKC0_0); also elsewhere on the board
/FPGA/SB8: U9.B8 (PT44B/-/PCLKC1_0); also elsewhere on the board
/FPGA/SB9: U9.D8 (PT42B/-/PCLKC1_1); also elsewhere on the board
/FPGA/SC0: U9.A9 (PT51A/+); also elsewhere on the board
/FPGA/SC1: U9.B9 (PT47A/+/GR_PCLK1_0); also elsewhere on the board
/FPGA/SC2: U9.C9 (PT47B/-/GR_PCLK1_1); also elsewhere on the board
/FPGA/SC3: U9.D9 (PT49A/+); also elsewhere on the board
/FPGA/SC4: U9.A10 (PT51B/-); also elsewhere on the board
/FPGA/SC5: U9.B10 (PT53A/+); also elsewhere on the board
/FPGA/SC6: U9.C10 (PT53B/-); also elsewhere on the board
/FPGA/SC7: U9.D10 (PT56A/+); also elsewhere on the board
/FPGA/SC8: U9.A11 (PT71A/+); also elsewhere on the board
/FPGA/SC9: U9.A12 (PT71B/-); also elsewhere on the board
/FPGA/SD0: U9.B11 (PT58A/+); also elsewhere on the board
/FPGA/SD1: U9.C11 (PT58B/-); also elsewhere on the board
/FPGA/SD2: U9.B12 (PT74A/+); also elsewhere on the board
/FPGA/SD3: U9.C12 (PT74B/-); also elsewhere on the board
/FPGA/SD4: U9.A14 (PT83B/-); also elsewhere on the board
/FPGA/SD5: U9.D12 (PT76A/+); also elsewhere on the board
/FPGA/SD6: U9.A13 (PT83A/+); also elsewhere on the board
/FPGA/SD7: U9.B13 (PT78A/+); also elsewhere on the board
/FPGA/SD8: U9.C13 (PT78B/-); also elsewhere on the board
/FPGA/SD9: U9.D13 (PT80A/+); also elsewhere on the board
/FPGA/SE0: U9.B15 (PR11B/-/URC_GPLL0C_IN/HS/RDQ17); also elsewhere on the board
/FPGA/SE1: U9.B16 (PR11A/+/URC_GPLL0T_IN/HS/RDQ17); also elsewhere on the board
/FPGA/SE2: U9.C15 (PR14B/-/HS/RDQ17); also elsewhere on the board
/FPGA/SE3: U9.C16 (PR14A/+/HS/RDQ17); also elsewhere on the board
/FPGA/SE4: U9.D16 (PR17A/+/HS/RDQS17); also elsewhere on the board
/FPGA/SE5: U9.E16 (PR20D/-/RDQ17); also elsewhere on the board
/FPGA/SE6: U9.E15 (PR17B/-/HS/RDQSN17); also elsewhere on the board
/FPGA/SE7: U9.F15 (PR20C/+/RDQ17); also elsewhere on the board
/FPGA/SE8: U9.E14 (PR14C/+/RDQ17); also elsewhere on the board
/FPGA/SE9: U9.F16 (PR23A/+/HS/RDQ29); also elsewhere on the board
/FPGA/SF0: U9.L16 (PR35A/+/PCLKT3_1/HS/RDQ41); also elsewhere on the board
/FPGA/SF1: U9.L15 (PR35B/-/PCLKC3_1/HS/RDQ41); also elsewhere on the board
/FPGA/SF2: U9.L14 (PR41C/+/RDQ41); also elsewhere on the board
/FPGA/SF3: U9.M16 (PR35C/+/PCLKT3_0/RDQ41); also elsewhere on the board
/FPGA/SF4: U9.M15 (PR35D/-/PCLKC3_0/RDQ41); also elsewhere on the board
/FPGA/SF5: U9.M14 (PR41D/-/RDQ41); also elsewhere on the board
/FPGA/SF6: U9.N16 (PR41A/+/HS/RDQS41); also elsewhere on the board
/FPGA/SF7: U9.P16 (PR44A/+/HS/RDQ41); also elsewhere on the board
/FPGA/SF8: U9.R16 (PR44B/-/VREF1_3/HS/RDQ41); also elsewhere on the board
/FPGA/SF9: U9.T15 (PR59D/-/RDQ65); also elsewhere on the board
/FPGA/SPI.CLK: U9.R2 (PL59C/+/LDQ65); also elsewhere on the board
/FPGA/SPI.CS: U9.T2 (PL59D/-/LDQ65); also elsewhere on the board
/FPGA/SPI.MISO: U9.R1 (PL44B/-/VREF1_6/HS/LDQ41); also elsewhere on the board
/FPGA/SPI.MOSI: U9.P1 (PL44A/+/HS/LDQ41); also elsewhere on the board
/FPGA/W5500.MISO: U9.E1 (PL20D/-/LDQ17); also elsewhere on the board
/FPGA/W5500.MOSI: U9.D1 (PL17A/+/HS/LDQS17); also elsewhere on the board
/FPGA/W5500.SCLK: U9.F1 (PL23A/+/HS/LDQ29); also elsewhere on the board
/FPGA/W5500.nINT: U9.C1 (PL14A/+/HS/LDQ17); also elsewhere on the board
/FPGA/W5500.nRST: U9.B1 (PL11A/+/ULC_GPLL0T_IN/HS/LDQ17); also elsewhere on the board
/FPGA/W5500.nSCS: U9.G1 (PL29A/+/GR_PCLK7_1/HS/LDQS29); also elsewhere on the board
/RP2040 JTAG/JTAG.RST: J8.10, R48.2, U9.R9 (PROGRAMN); also elsewhere on the board
/RP2040 JTAG/JTAG.RX: U9.T3 (PL62D/-/LDQ65); also elsewhere on the board
/RP2040 JTAG/JTAG.TCK: J8.4, R49.1, U9.T10 (TCK); also elsewhere on the board
/RP2040 JTAG/JTAG.TDI: J8.8, U9.R11 (TDI); also elsewhere on the board
/RP2040 JTAG/JTAG.TDO: J8.6, U9.M10 (TDO); also elsewhere on the board
/RP2040 JTAG/JTAG.TMS: J8.2, U9.T11 (TMS); also elsewhere on the board
/RP2040 JTAG/JTAG.TX: U9.R3 (PL62B/-/HS/LDQ65); also elsewhere on the board
/Slots/SlotEN: U9.T14 (PR62D/-/RDQ65); also elsewhere on the board
GND: C47.2, C48.2, C49.2, C50.2, C51.2, C52.2, C53.2, C54.2, C55.2, C56.2, C57.2, C58.2, C59.2, C60.2, C61.2, C62.2, C63.2, C64.2, C65.2, C66.2, C67.2, J8.3, J8.5, J8.9, J10.3, J10.4, Q1.2 (S), Q2.2 (S), Q3.2 (S), R44.2, R45.2, R49.2, U9.A1 (GND[27]), U9.A16 (GND[27]), U9.D2 (GND[27]), U9.D15 (GND[27]), U9.F8 (GND[27]), U9.F9 (GND[27]), U9.G8 (GND[27]), U9.G10 (GND[27]), U9.H1 (GND[27]), U9.H8 (GND[27]), U9.H9 (GND[27]), U9.H10 (GND[27]), U9.H16 (GND[27]), U9.J8 (GND[27]), U9.J9 (GND[27]), U9.J10 (GND[27]), U9.K6 (GND[27]), U9.K7 (GND[27]), U9.K8 (GND[27]), U9.K9 (GND[27]), U9.K10 (GND[27]), U9.N2 (GND[27]), U9.N15 (GND[27]), U9.T1 (GND[27]), U9.T5 (GND[27]), U9.T12 (GND[27]), U9.T16 (GND[27]), U10.4 (GND), X1.2 (GND); also elsewhere on the board
unnamed: D10.2 (A), R50.2
unnamed: D10.1 (K), Q1.3 (D)
unnamed: D11.2 (A), R51.2
unnamed: D11.1 (K), Q2.3 (D)
unnamed: D12.2 (A), R52.2
unnamed: D12.1 (K), Q3.3 (D)
unnamed: R44.1, U9.N10 (CFG_0)

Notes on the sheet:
WTF?
WTF? CLK?
Pin numbering matches default socket footprint


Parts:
C21, C24, C25, C27, C28, C29, C30, C31, C32: 0.1uF; C_0603_1608Metric; MPN CC0603KRX7R9BB104; LCSC# C14663
C22, C23: 10pF; C_0603_1608Metric; MPN CC0603JRNPO9BN100; LCSC# C106245
C26: 1uF; C_0603_1608Metric; MPN CL10A105KA8NNNC; LCSC# C5673
D3: LED_GREEN; LED_0603_1608Metric; MPN SZYY0603YG; LCSC# C434423
D4: LED_RED; LED_0603_1608Metric; MPN SZYY0603R; LCSC# C434419
D5: LED_BLUE; LED_0603_1608Metric; MPN XL-1608UBC-04; LCSC# C965807
D6, D7, D8: BSD5C031V; D_SOD-523; MPN BSD5C031V; LCSC# C151984
D9: DSS34; D_SOD-123F; MPN DSS34; LCSC# C511866
FB6: FB_100R_3A; L_0603_1608Metric; MPN UPZ1608E101-3R0TF; LCSC# C96995
J2, J5: PIN_HEADER_3V; PinHeader_1x03_P2.54mm_Vertical; MPN C49257; LCSC# C49257
J3: TYPE-C-31-M-12; USB_C_Receptacle_HRO_TYPE-C-31-M-12; MPN TYPE-C-31-M-12; LCSC# C165948
J4: Conn_02x05_Odd_Even; PinHeader_2x05_P2.54mm_Vertical
JP1: SolderJumper_2_Open; SolderJumper-2_P1.3mm_Open_RoundedPad1.0x1.5mm
R16, R18, R19, R28: 1K; R_0603_1608Metric; MPN RC0603FR-071KL; LCSC# C22548
R17, R23, R27: 10K; R_0603_1608Metric; MPN RC0603FR-0710KL; LCSC# C98220
R20, R21, R22: 5.11K; R_0603_1608Metric; MPN RC0603FR-075K11L; LCSC# C112314
R26: 100K; R_0603_1608Metric; MPN RC0603FR-075K11L; LCSC# C112314
SW1: SW_PUSH_SMALL; SW_SPST_AR02016; MPN TS-1088-AR02016; LCSC# C720477
TP7, TP8, TP9: TP_1MM; TestPoint_Pad_D1.0mm
U5: W25Q16JVSS; SOIC-8_5.23x5.23mm_P1.27mm; MPN W25Q16JVSSIQ; LCSC# C82317
U6: USBLC6-4SC6; SOT-23-6; MPN USBLC6-4SC6; LCSC# C5197386
U7: RP2040; RP2040-QFN-56; MPN RP2040; LCSC# C2040
Y1: Crystal_12MHz; Crystal_SMD_2520-4Pin_2.5x2.0mm; MPN TXM12M0004252DBCEO00T; LCSC# C284154

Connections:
+3V3: C21.1, C28.1, C29.1, C30.1, C31.1, C32.1, FB6.1, J4.1, R17.2, U5.8 (VCC), U7.1 (IOVDD), U7.10 (IOVDD), U7.22 (IOVDD), U7.33 (IOVDD), U7.42 (IOVDD), U7.44 (VREG_IN), U7.48 (USB_VDD), U7.49 (IOVDD); also elsewhere on the board
+5V: D9.1 (K); also elsewhere on the board
+24V: R26.2; also elsewhere on the board
/FPGA/SPI.CLK: U7.4 (GPIO2); also elsewhere on the board
/FPGA/SPI.CS: U7.7 (GPIO5); also elsewhere on the board
/FPGA/SPI.MISO: U7.6 (GPIO4); also elsewhere on the board
/FPGA/SPI.MOSI: U7.5 (GPIO3); also elsewhere on the board
/RP2040 JTAG/1V1_RP2040: C24.1, C25.1, C26.1, U7.23 (DVDD), U7.45 (VREG_VOUT), U7.50 (DVDD)
/RP2040 JTAG/DBG_UART_RX: D7.2 (A2), J5.3, U7.3 (GPIO1)
/RP2040 JTAG/DBG_UART_TX: D6.2 (A2), J5.1, U7.2 (GPIO0)
/RP2040 JTAG/FLASH_CLK: U5.6 (CLK), U7.52 (QSPI_SCLK)
/RP2040 JTAG/FLASH_CS: R16.1, R17.1, U5.1 (~CS), U7.56 (QSPI_SS)
/RP2040 JTAG/GPIO6: J4.5, U7.8 (GPIO6)
/RP2040 JTAG/GPIO7: J4.7, U7.9 (GPIO7)
/RP2040 JTAG/GPIO10: J4.9, U7.13 (GPIO10)
/RP2040 JTAG/GPIO11: J4.4, U7.14 (GPIO11)
/RP2040 JTAG/GPIO12: J4.6, U7.15 (GPIO12)
/RP2040 JTAG/GPIO13: J4.8, U7.16 (GPIO13)
/RP2040 JTAG/JTAG.RST: U7.31 (GPIO20); also elsewhere on the board
/RP2040 JTAG/JTAG.RX: U7.12 (GPIO9); also elsewhere on the board
/RP2040 JTAG/JTAG.TCK: U7.29 (GPIO18); also elsewhere on the board
/RP2040 JTAG/JTAG.TDI: U7.27 (GPIO16); also elsewhere on the board
/RP2040 JTAG/JTAG.TDO: U7.28 (GPIO17); also elsewhere on the board
/RP2040 JTAG/JTAG.TMS: U7.30 (GPIO19); also elsewhere on the board
/RP2040 JTAG/JTAG.TRST: U7.32 (GPIO21)
/RP2040 JTAG/JTAG.TX: U7.11 (GPIO8); also elsewhere on the board
/RP2040 JTAG/LED_BLUE: D5.2 (A), U7.34 (GPIO22)
/RP2040 JTAG/LED_GRN: D3.2 (A), U7.35 (GPIO23)
/RP2040 JTAG/LED_RED: D4.2 (A), U7.37 (GPIO25)
/RP2040 JTAG/SWCLK: J2.3, TP7.1, U7.24 (SWCLK)
/RP2040 JTAG/SWD: J2.1, TP8.1, U7.25 (SWD)
/RP2040 JTAG/USB_D_N: J3.A7 (D-), J3.B7 (D-), U6.4 (I/O3), U7.46 (USB_DM)
/RP2040 JTAG/USB_D_P: J3.A6 (D+), J3.B6 (D+), U6.6 (I/O4), U7.47 (USB_DP)
/RP2040 JTAG/VBUS_SENSE: R22.1, R23.1, U7.36 (GPIO24)
/RP2040 JTAG/VIN_SENSE: D8.2 (A2), R26.1, R27.1, U7.41 (GPIO29_ADC3)
GND: C21.2, C22.1, C23.1, C24.2, C25.2, C26.2, C27.2, C28.2, C29.2, C30.2, C31.2, C32.2, D6.1 (A1), D7.1 (A1), D8.1 (A1), J2.2, J3.A1 (GND), J3.A12 (GND), J3.B1 (GND), J3.B12 (GND), J3.S1 (SHIELD), J4.10, J5.2, JP1.1 (A), R18.2, R19.2, R20.1, R21.2, R23.2, R27.2, R28.2, SW1.1, TP9.1, U5.4 (GND), U6.2 (GND), U7.19 (TESTEN), U7.57 (GND), Y1.1, Y1.3; also elsewhere on the board
unnamed: D3.1 (K), R18.1
unnamed: D4.1 (K), R19.1
unnamed: D5.1 (K), R28.1
unnamed: J3.A5 (CC1), R20.2
unnamed: J3.B5 (CC2), R21.1
unnamed: JP1.2 (B), U7.26 (RUN)
unnamed: R16.2, SW1.2 (A)
unnamed: U5.5 (DI(IO0)), U7.53 (QSPI_SD0)
unnamed: U5.2 (DO(IO1)), U7.55 (QSPI_SD1)
unnamed: U5.3 (IO2), U7.54 (QSPI_SD2)
unnamed: U5.7 (IO3), U7.51 (QSPI_SD3)
unnamed: C27.1, FB6.2, U7.43 (ADC_AVDD)
unnamed: C22.2, U7.20 (XIN), Y1.2
unnamed: C23.2, U7.21 (XOUT), Y1.4
VBUS: D9.2 (A), J3.A4 (VBUS), J3.A9 (VBUS), J3.B4 (VBUS), J3.B9 (VBUS), R22.2, U6.5 (VBUS)


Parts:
C1: 10uF; C_0805_2012Metric; MPN GRM21BR6YA106ME43L; LCSC# C361063
C2, C3: 10uF; C_0805_2012Metric; MPN GRM21BR61H106KE43L; LCSC# C440198
C4, C5, C13, C14: 0.1uF; C_0603_1608Metric
C6, C7: 120pF; C_0603_1608Metric
C8, C9: 0.012uF; C_0603_1608Metric
C10: DNP; C_0603_1608Metric
C11: 10uF/35V; C_0805_2012Metric; MPN GRM21BR6YA106ME43L; LCSC# C361063
C12: 0.1uF; C_0603_1608Metric; MPN CC0603KRX7R9BB104; LCSC# C14663
C15, C16, C17, C18: 47uF; C_0805_2012Metric; MPN GRM21BR61H106KE43L; LCSC# C440198
C19, C20: 1uF; C_0603_1608Metric
D1: DSS34; D_SOD-123F; MPN DSS34; LCSC# C511866
D2: LED_RED; LED_0603_1608Metric; MPN SZYY0603R; LCSC# C434419
FB1, FB2, FB3, FB4, FB5: FB_100R_3A; L_0603_1608Metric; MPN UPZ1608E101-3R0TF; LCSC# C96995
H1, H2, H3, H4: MH_3.2mm; MountingHole_3.2mm_M3_Pad_Via
J1: TERM-BLK-2H; PhoenixContact_MC_1,5_2-G-3.5_1x02_P3.50mm_Horizontal; MPN KF2EDGR-3.5-2P; LCSC# C441171
L1: MLP2012S4R7MT0S1; L_0805_2012Metric; MPN MLP2012S4R7MT0S1; LCSC# C87543
L2, L3: PSPMAA0805-220M-ANP; SMD_INDUCTOR_8x8.5x5mm; MPN PSPMAA0805-220M-ANP; LCSC# C2962887
R1: 10K; R_0603_1608Metric
R2, R3, R5, R7, R10: 47K; R_0603_1608Metric
R4, R6: 220K; R_0603_1608Metric
R8, R9: 3.47K; R_0603_1608Metric
R11: 56.2K; R_0603_1608Metric; MPN RC0603FR-0710KL; LCSC# C98220
R12, R14: 100K; R_0603_1608Metric
R13: 19.1K; R_0603_1608Metric
R15: 32K; R_0603_1608Metric
TP1, TP2, TP3, TP4, TP5, TP6: TP_1MM; TestPoint_Pad_D1.0mm
U1: TD6811; SOT-23-5; MPN TD6811; LCSC# C189486
U2, U3: TPS54335ADDAR; SOIC-8-1EP_3.9x4.9mm_P1.27mm_EP2.29x3mm_ThermalVias; MPN TPS54335ADDAR; LCSC# C58928
U4: NCP114ASN250T1G; SOT-23-5; MPN NCP114ASN250T1G; LCSC# C892030
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

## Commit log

2024-08-17 Initial commit, controller schematic and layout done
    [fpga.kicad_sch, power.kicad_sch, rioctrl-controller.kicad_pcb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]
2024-08-17 Initial schematic and layout of rioctrl-backplane
    [inputs.kicad_sch, rioctrl-backplane.kicad_pcb, rioctrl-backplane.kicad_sch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]
2024-08-18 Ditch the separate backplane board, increase the slot bitwidth to 12
    [fpga.kicad_sch, inputs.kicad_sch, power.kicad_sch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]
2024-08-19 Initial schematic and layout of stepdir4
    [rioctrl-stepdir4.kicad_pcb, rioctrl-stepdir4.kicad_sch, slot.kicad_sch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]
2024-08-19 rioctrl-stepdir4: pass ERC and DRC
    [rioctrl-stepdir4.kicad_pcb, slot.kicad_sch, stepdir.kicad_sch]
2024-08-19 rioctrl-stepdir4: cleanup schematics
    [stepdir.kicad_sch]
2024-08-19 Add symlinks to hadv-kicad-lib in each subdirectory
2024-08-19 Label axes on stepdir
    [rioctrl-stepdir4.kicad_pcb, rioctrl-stepdir4.kicad_sch, stepdir.kicad_sch]
2024-08-20 Add RJ45 screw terminal breakout, Lichuan LC10 breakout
    [lichuan-lc10.kicad_pcb, lichuan-lc10.kicad_sch, rj45-screw-terminals.kicad_pcb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]
2024-08-25 Add rioctrl-quadenc4 initial design
    [quadenc.kicad_sch, rioctrl-quadenc4.kicad_pcb, rioctrl-quadenc4.kicad_sch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]
2024-08-25 Fix ERC, add title information to sch, add initial version of build scripts
    [fpga.kicad_sch, lichuan-lc10.kicad_sch, power.kicad_sch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]
2024-08-28 Add initial version of rioctrl-shiftio
    [di4.kicad_sch, digital_output.kicad_sch, do4.kicad_sch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]
2024-08-29 Fill in BOM (LCSC#)
    [di4.kicad_sch, digital_output.kicad_sch, do4.kicad_sch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]
2024-08-29 Add short documentation for the controller and modules
    [lichuan-lc10.kicad_pcb, rj45-screw-terminals.kicad_pcb]
2024-08-29 Release outputs
    [bom-lichuan-lc10.csv, bom-rioctrl-controller.csv, bom-rioctrl-quadenc4.csv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]
2024-08-31 Update 3D model of RJ45 connector
    [lichuan-lc10.kicad_pcb, rioctrl-quadenc4.kicad_pcb, rioctrl-stepdir4.kicad_pcb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]
2024-08-31 Update footprints for terminal blocks
    [rioctrl-shiftio.kicad_pcb, rj45-screw-terminals.kicad_pcb]
2024-08-31 Regenerate outputs with more 3D models
    [input_shiftreg.kicad_sch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]
2024-08-31 Add forgotten series resistor for 24V output transistors in rioctrl-stepdir4
    [bom-rioctrl-stepdir4.csv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]
2024-08-31 Add pulldown for SlotEN signal
    [bom-rioctrl-controller.csv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]
2024-08-31 Add netlist parser to generate slot descriptions for riocore
2024-09-21 Fix minor issues in rioctrl-controller, release v1.1
    [fpga.kicad_sch, rp2040.kicad_sch]
2024-09-22 Update build scripts to generate ibom as well
    [lichuan-lc10-CmtUser.gbr, lichuan-lc10-CuBottom.gbl, lichuan-lc10-CuTop.gtl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]
2024-09-22 Add rioctrl-controller v1.1 outputs
    [bom-rioctrl-controller.csv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]
2024-09-22 Release rioctrl-stepdir v1.1
    [bom-rioctrl-stepdir4.csv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]
2024-09-22 rioctrl-shiftio: change the part number of 1 ohm resistor (previously, an 0603 resistor was specified for 0805 footprint)
    [bom-rioctrl-shiftio.csv, digital_output.kicad_sch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]
2024-09-22 Add breakouts/ditron-dc11-encoder
    [bom-ditron-dc11-encoder.csv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]
2024-09-22 Update breakouts/ditron-dc11-encoder: enlarge the PCB slightly
    [ditron-dc11-encoder-CmtUser.gbr, ditron-dc11-encoder-CuBottom.gbl, ditron-dc11-encoder-CuTop.gtl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]
2024-09-25 Add pick&place position files to outputs
    [ditron-dc11-encoder-CmtUser.gbr, ditron-dc11-encoder-CuBottom.gbl, ditron-dc11-encoder-CuTop.gtl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]
2025-03-26 Add initial spindle card design: schematics sort of done
    [analog_out.kicad_sch, quadenc.kicad_sch, rioctrl-spindle.kicad_pcb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]
2025-03-26 rioctrl-spindle v1.0 release
    [analog_out.kicad_sch, bom-rioctrl-spindle.csv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]
2025-05-13 Add readme for spindle module
